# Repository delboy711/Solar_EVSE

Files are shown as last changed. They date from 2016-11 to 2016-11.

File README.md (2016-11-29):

# Solar EVSE
## Description
 This project is intended to manage the charging of an electric car so that the charging current is varied in accordance with available
solar power from a PV array.

## Introduction
Electric cars require an EVSE (Electric Vehicle Supply Equipment) to connect to the domestic electricity supply.  It is the responsibility
 of the EVSE to signal to the car the maximum current it is allowed to draw based on factors like the rating of the domestic wiring, and the cable 
connecting the vehicle to the EVSE.  A smart controller inside the EVSE called an EPC (Electronic Protocol Controller) performs the function by setting the duty cycle on a 12V 
pilot signal sent to the car via the charging cable.  One of the leading models of EPC is manufactured by <a href="https://ecoharmony.co.uk/collections/evse-protocol-controller/products/viridianev-tethered-epc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">Viridian</a> (sometimes labelled as MainPine)
 What makes the Viridian EPC interesting to a DIYer is the fact that the available current signalled to the car can be controlled by applying a voltage on a control pin
 on the Viridian EPC.
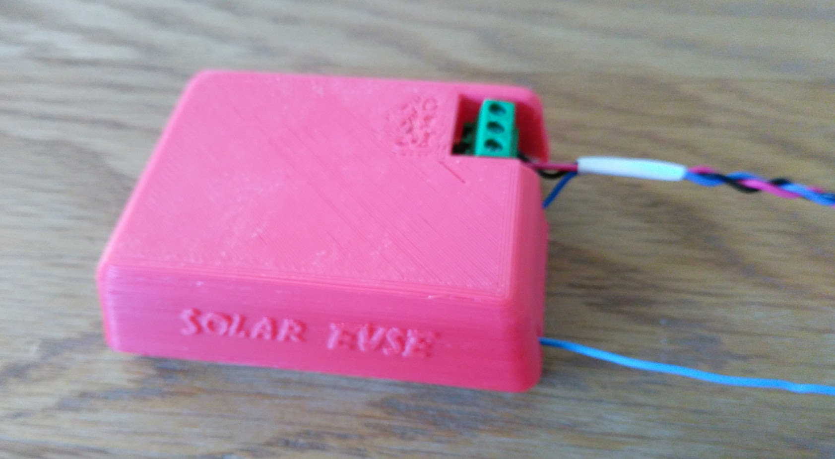
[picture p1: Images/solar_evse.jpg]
Solar EVSE

This project is for an Arduino based device to set that control voltage based on a calculation of available solar power made by an <a href="https://openenergymonitor.org/emon/">OpenEnergyMonitor</a> system, and transmitted
 to the Arduino via a radio link.  The Arduino takes no part in the decision making process. It merely applies the voltage dictated by OpenEnergyMonitor.  The Viridian
 EPC has its own fail safes to prevent an unsafe current being signalled to the vehicle.

## Hardware required is
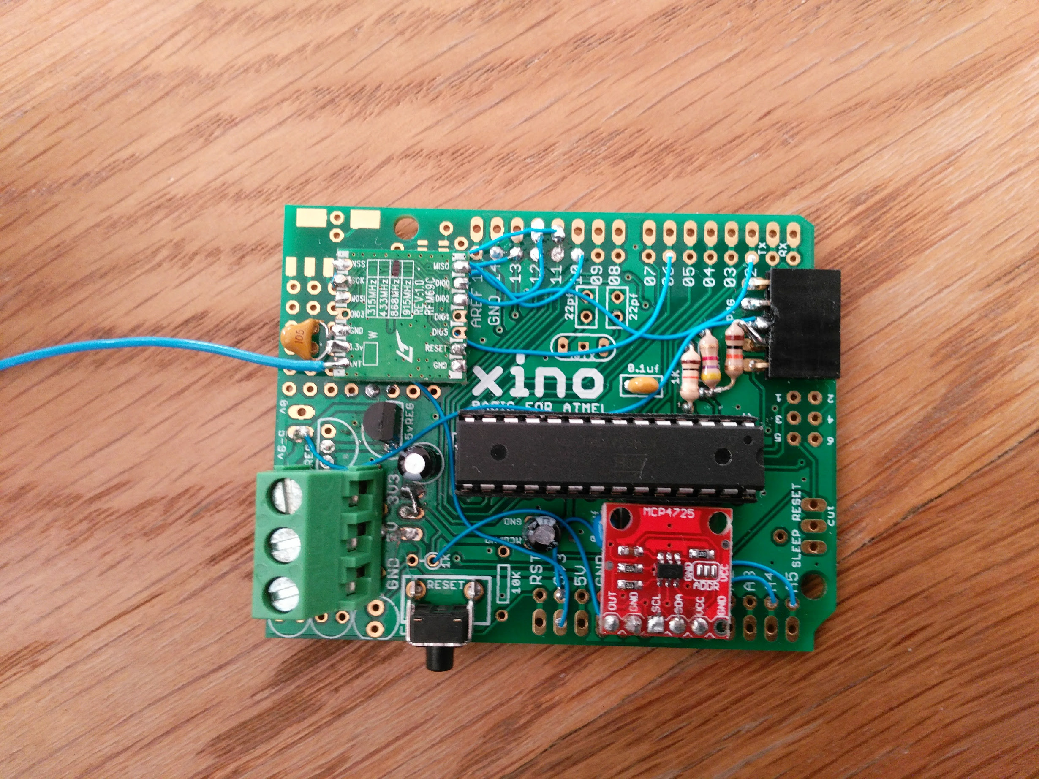
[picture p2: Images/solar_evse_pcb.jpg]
### Arduino Uno -
 or clone, or stripboard with Atmel328P  No crystal required.  I used a <a href="https://nathan.chantrell.net/20110910/xino-basic-arduino-clone/">Xino</a> which is a minimalist Arduino clone with no usb interface, and I 
modfied it to run off 3.3V power which has the advantage of allowing finer control of the Digital to Analogue Converter, and means no step down resistors are required
  for the RFM69CW radio module which requires a 3.3V supply.  By burning a new bootloader into the Atmega328P chip I was able to run it using the <a href="https://www.arduino.cc/en/Tutorial/ArduinoToBreadboard">8MHz internal clock</a> and so saved on the cost of a crystal, and reduced power consumption. Power was drawn from 
the 5V rail of the Viridian EPC itself by wiring in an extra screw connector into the housing of the EPC. Using a Xino at 8MHz the current requirement is 20mA.
* **MCP4725** Digital to Analogue converter module. It is very cheap to buy MCP4725 chips on ebay, ready mounted on a pcb which saves the trouble of trying to solder
surface mount components.
* **RFM69CW** 433MHz or 868MHz radio module. This is the radio module used in the OpenEnergyMonitor project. They are cheap on ebay.
* **Viridian** <a href="https://ecoharmony.co.uk/collections/evse-protocol-controller/products/viridianev-tethered-epc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">Tethered EPC</a>  
                Viridian make their own EVSEs, but I was unable to buy one at a sensible price so instead I bought a <a href="http://www.rolecserv.com/ev-charging/product/EV-Charging-Points-For-The-Home">Rolec EVSE</a> and replaced the Rolec EPC with a Viridian.
Since both the Rolec and Viridian EPCs are DIN rail mounted modules this was a simple exchange.
* **EmonPi or Emonbase** from OpenEnergyMonitor.org
  
## Arduino Libraries required
* **Jeelib**
* **Wire**
* **Adafruit_MCP4725**
  
## Software required
* **Emonhub**
Part of EmonPi or Emonbase. Used to transmit commands over radio link.<br>
A patch is required for emonhub to allow it to transmit control messages to Solar_EVSE. See GitHub for required patch to emonhub.
* **Node-Red**
Included as part of EmonPi.  Used to calculate Solar PV power PV available.
See Node-Red folder for an example flow.
  
## Operation
   This sketch is very simple. The process loops continually waiting for a packet ready flag
   from the RFM69CW radio unit.  When the packet arrives it is validated for CRC and correct address and a single integer
   variable is read.  If the variable has msb bit set, then it is a command to set a new default Power on Voltage for the DAC
   to use. If msb bit is zero it is a new command to set a voltage on the DAC.
   The voltage set on the DAC is passed to the Viridian EPC which uses it to vary the duty cycle
   of the Pilot signal given to an attached electric
   car, and so regulates the current drawn while charging.<br><br>

Installation notes are [here](INSTALLATION.md)

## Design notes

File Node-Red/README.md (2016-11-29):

# Example Node Red flow
In this file is an example flow for Node Red to control a Solar EVSE unit based on available solar power.
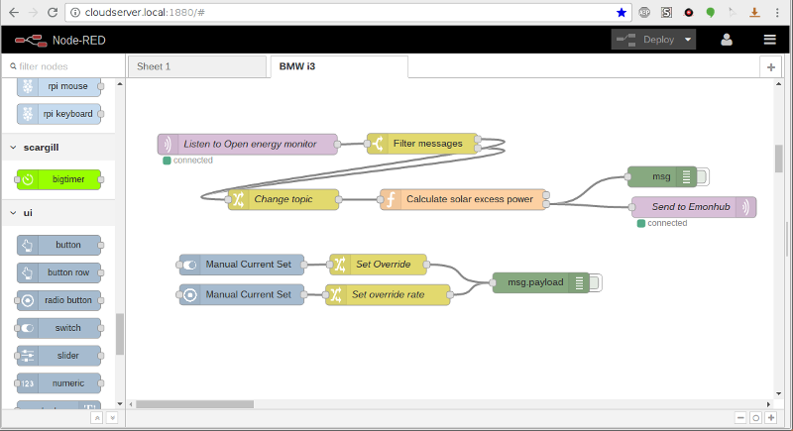
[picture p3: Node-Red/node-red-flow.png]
Node Red flow
To use the flow copy to clipboard and then import into Node Red. 
## Required Nodes
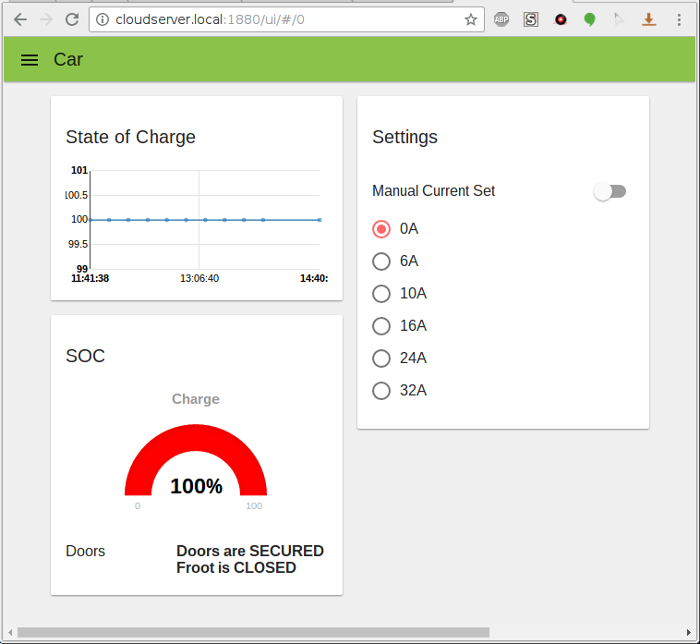
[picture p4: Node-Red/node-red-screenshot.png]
Node Red UI
 This example flow makes use of the [node-red-contrib-ui](https://flows.nodered.org/node/node-red-contrib-ui) node to create a simple user interface to override Open Energy Monitor,
 and set a fixed rate of charge to the vehicle.  In this screenshot are also visible a chart and dial showing vehicle state of charge, These items are not included in
 this flow, and are a separate project.
## Data format
This flow assumes that OpenEnergy Monitor has been configured to provide MQTT messages with the following topics.
* **SMASolar/ACOutputPhase1** - This topic has a payload of output from the solar panels in W. In my system I can read this figure directly from my SMA inverter via a python
 script and Bluetooth.
* **emon/solar_EVSE/car_power** - This topic has a payload of the power being consumed by the car in W.  In my system I derive it from a current sensing transformer
 attached to the EVSE power supply.
* **emon/solar_EVSE/house_power** - This topic has a payload of the total power being consumed in the house, including that consumed by the car.

The flow produces a single output with the topic **emonhub/tx/24/values** which represents the Voltage the Arduino based Solar_EVSE unit should 
 signal to the Viridian EPC. The stanza shown in the emonhub folder should be added to the emonhub.conf file so that emonhub knows what to do with the MQTT message,
 and the patch **EmonHubJeeInterfacer.patch** in the emonhub folder should be applied to emonhub so it can send packets to  remote nodes.
Be aware emonhub is very fussy about receiving properly formatted MQTT packets.  It will crash if it receives a malformed packet.

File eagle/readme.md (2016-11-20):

## Example Schematic
for Solar EVSE mounted on a shield expansion card for an Arduino Uno running at 5V
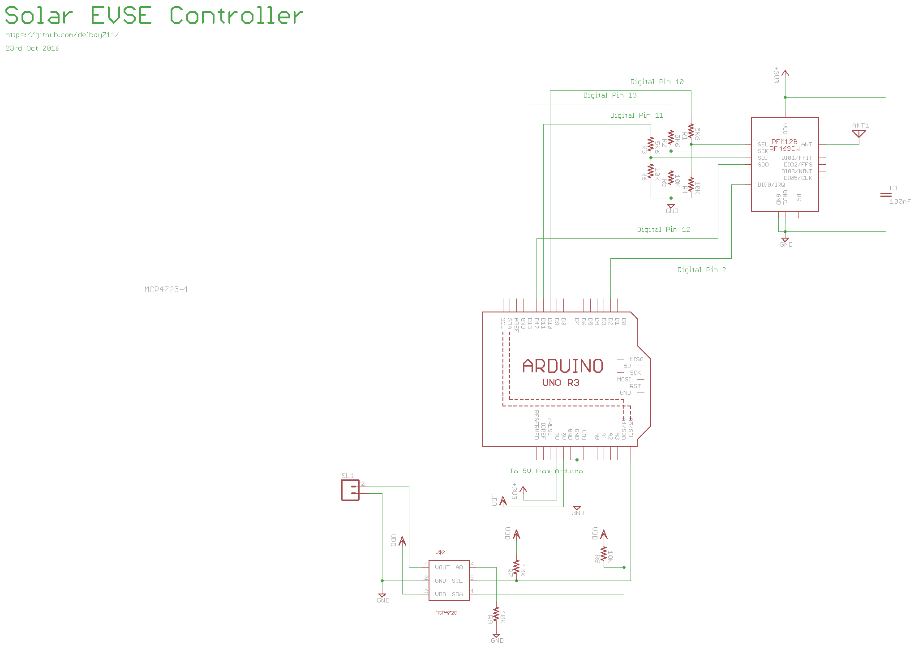
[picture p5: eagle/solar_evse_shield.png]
Arduino shield


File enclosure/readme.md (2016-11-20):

## Files
 for 3D printed enclosure for Solar_EVSE written in OpenSCAD

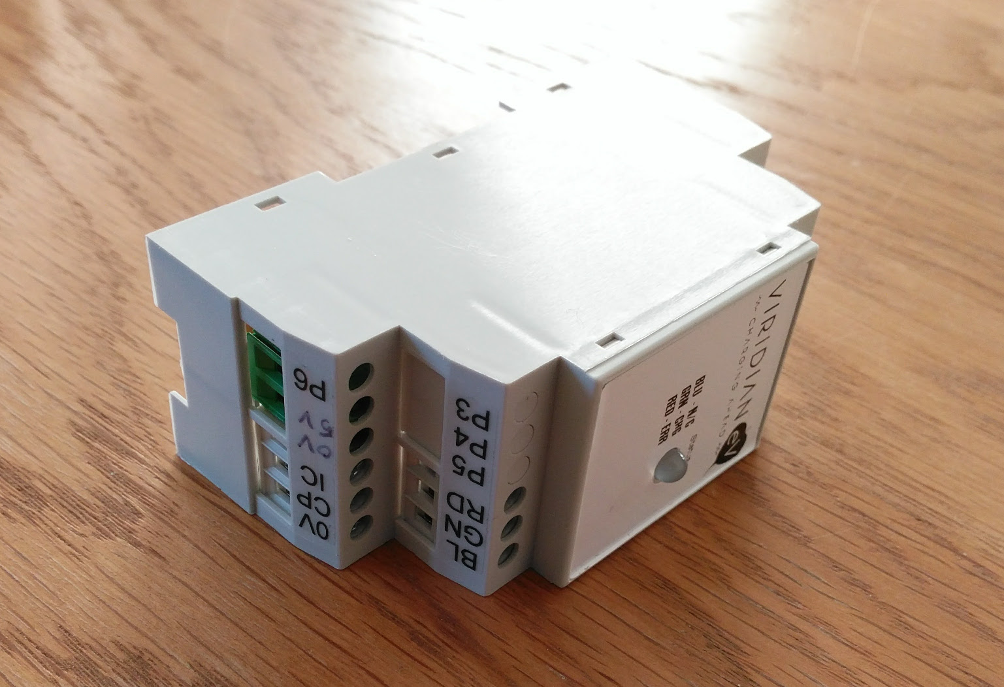
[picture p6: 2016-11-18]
Images/viridian_evse2.jpg

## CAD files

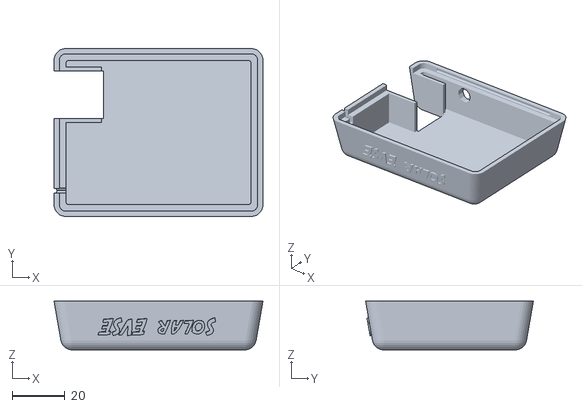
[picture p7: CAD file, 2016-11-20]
enclosure/solarEVSE_top.stl
79.0 x 63.5 x 18.5

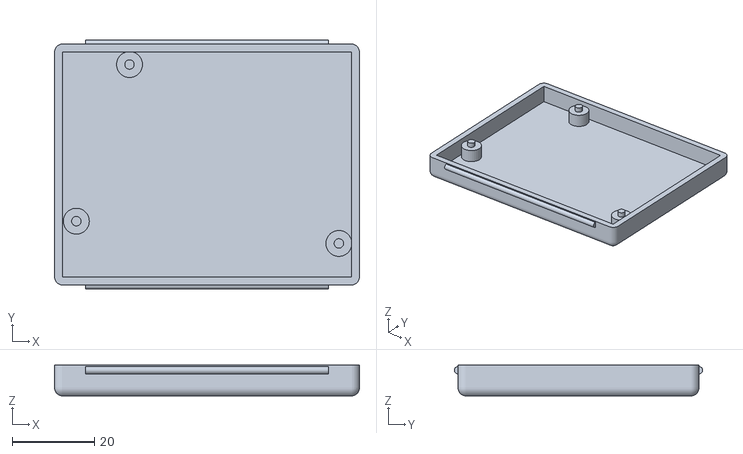
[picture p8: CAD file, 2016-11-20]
enclosure/solarEVSE_bottom.stl
74.0 x 60.3 x 7.49

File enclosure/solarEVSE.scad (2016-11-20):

//
// Arduino Uno
//
// Based on a design by Egil Kvaleberg, 8 Aug 2015
// Remixed by delboy711 21/08/2016

//
// notes:
// design origin is middle of PCB
//



// Set part = "all" to see both top and bottom parts
// Set part = "top" to see just the top part
// Set part = "bottom" to see just the bottom part
// Set part = "demo" to see both parts fitted together
part = "all"; // [ top, bottom, all, demo ]
// Is the Arduino a Uno (USB, and power socket), or a Xino (bare bones no usb or power socket)
// See https://www.wirelessthings.net/xino-basic-for-atmel-atmega-avr-arduino-compatible-kit
device = "Xino";  // [ Uno. Xino ]
// Select feature options
have_emontx_shield =0 ; //Is fitted with an emontx shield card
have_text = 1; //  Writing on side
text_="Solar EVSE";   // Text to write on side
font_size= 7;  // Text font size
have_pcb_fixings = 0; // 
have_snaplock = 1;   // snaplocks on edges
have_bottom_vents = 0;  // Ventilation slots on bottom
have_top_vents = 0;  // Ventilation slots on top
have_cable_outlet= 1; // Has hole for cable outlet
have_screwblock=1;    //Opening for screwblock in lid


/* [Hidden] */
mil2mm = 0.0254;
pcb = [69, 53.5, 1.5]; // main board 
extra_width = 0;   
extra_depth = 0;   // extra space below pcb
extra_length = (have_emontx_shield ? 26 : 0); // extra length Longer with emontx shield fitted
extra_height = (have_emontx_shield ? 9 : 0);   // extra space above pcb taller with emontx shield 
pcb2floor = 4.0 + extra_depth; //  
pcb2roof = 14 + extra_height; //   

pcbmntdia = 2.3; // mounting holes
pcbmntdx= [pcb[0]/2 - 2.5, (device == "Uno" ? 14.5 : 2.8)-pcb[0]/2, pcb[0]/2 - 2.3, pcb[0]/2 - 53.3];  //location of mount holes
pcbmntdy= [7.6 - pcb[1]/2, (device == "Uno" ? 2.8 : 13)-pcb[1]/2, 9.1, pcb[1]/2 - 2.5];

breakaway = 0.3; // have hidden hole for screw, 0 for no extra pegs 
usbsy = 10.5; // core
usbframe = 1.0; // frame
usbsz = 10 + 0.5;
usb1dy = pcb[1]/2 - 15.0;
powerpsx = 9; // power plug width 
powerpsz = 14.0; // plug height
powerssx = 9.9; // power socket width 
powerssz = 10.0; // socket height
powerdz = -1.7; // for plug 
powerdy = 8.8- pcb[1]/2; // 
emonacdz = -3;   // AC power socket of emontx shield
emonacdx = pcb[0]/2 -1.5;
frame_w = 2.5; // width of lip for frame 
snap_dia = 1.8; // snap lock ridge diameter
snapedges = false; // snap lock on all edges or just long ones
//snap_len = 40.0; // snap lock length - no longer used DJ
tol = 0.5; // general tolerance

wall = 2; // general wall thickness  was 1.2 dj
thinwall = 1;   // was 0.4 dj
corner_r = wall; // casing corner radius
corner2_r = wall+tol+wall; // corners of top casing
d = 0.01;
 

module c_cube(x, y, z) {
	translate([-x/2, -y/2, 0]) cube([x, y, z]);
}

module cr_cube(x, y, z, r) {
	hull() {
		for (dx=[-1,1]) for (dy=[-1,1]) translate([dx*(x/2-r), dy*(y/2-r), 0]) cylinder(r=r, h=z, $fn=20);
	}
}

module cr2_cube(x, y, z, r1, r2) {
	hull() {
		for (dx=[-1,1]) for (dy=[-1,1]) translate([dx*(x/2-r1), dy*(y/2-r1), 0]) cylinder(r1=r1, r2=r2, h=z, $fn=20);
	}
}

module bottom() {
	module snap2(ex, both) {
		if (both) translate([pcb[0]/2+tol+wall+ex+extra_length, -(pcb[1]+extra_width-10)/2, wall+pcb2floor+pcb[2]-frame_w/2]) rotate([-90, 0, 0]) cylinder(r=snap_dia/2, h=pcb[1]+extra_width-10, $fs=0.3);
		translate([-(pcb[0]-10)/2, -(pcb[1]/2+tol+wall+extra_width/2), wall+pcb2floor+pcb[2]-frame_w/2]) rotate([0, 90, 0]) cylinder(r=snap_dia/2, h=pcb[0]+extra_length-10, $fs=0.3);
	}
    module plugs(extra) { 
        z0 = wall+pcb2floor+pcb[2];
    }
    module plugs_add() { 
        z0 = wall+pcb2floor+pcb[2];
    }

	module add() {
		hull () for (x = [-1, 1]) for (y = [-1, 1])
			translate([x*(pcb[0]/2+tol+wall-corner_r) + (x>0 ? extra_length : 0), y*(pcb[1]/2+tol+wall+extra_width/2-corner_r), corner_r]) {
				sphere(r = corner_r, $fs=0.3);
				cylinder(r = corner_r, h = wall+pcb2floor+pcb[2]-corner_r, $fs=0.3);
		}
		if (have_snaplock) {
            snap2(0, snapedges);
            rotate([0, 0, 180]) translate([-extra_length,0,0]) snap2(0, snapedges);
        }
	}
	module sub() {
        module pedestal(x, hg, dia) {
            translate([pcbmntdx[x], pcbmntdy[x], wall]) {
				cylinder(r = dia/2+wall, h = hg, $fs=0.2);
                // pegs through pcb mount holes
                if (breakaway > 0) translate([0, 0, hg]) 
                        cylinder(r = dia/2 , h = pcb[2]+d, $fs=0.2);
            }
        }
		difference () {
			// pcb itself
			translate([-(pcb[0]/2+tol), -(pcb[1]/2+tol)-extra_width/2, wall])
				cube([2*tol+pcb[0]+extra_length, 2*tol+pcb[1]+extra_width, pcb2floor+pcb[2]+d]);
			// less pcb mount pedestals 
            for (x = (device=="Xino" ? [0,1,3] :[0:3]))  // leave out one pedestal if xino
                pedestal(x, pcb2floor, pcbmntdia);
            
            // Stop card moving
            if (extra_length > 0 ) translate([pcb[0]/2+0.7,-13,-pcb2floor+3]) cube([3,16,10]);
		}
        
        
        plugs(tol);
        
        
        // DJ Add bottom vents
        if ( have_bottom_vents ) 
            for ( dx=[-4 : 4] ) for ( dy=[-1, 1] ) translate([dx*7, dy*(pcb[1]/2-14), 0]) cube([2, pcb[1]/2-6, 2*wall], center=true);

        
	}
	difference () {
		add();
		sub();
	}
    plugs_add();

    if (part=="all" || part=="demo")  {
       if (device == "Uno") color("LightPink", 0.6) translate([-34,-26.5,6+extra_depth]) scale([10,10,10]) rotate([90,0,0])  import(file="arduino_pcb.stl");
       if (have_emontx_shield) color("LightBlue", 0.6) translate([-12,-26.5,18.5+extra_depth]) scale([0.001,0.001,0.001]) import("emontxshield.stl");
    }
 
}

// Z base is top of pcb
module top() {
	module snap2(ex, both) {
		if (both) translate([pcb[0]/2+tol+wall+ex+extra_length, -(pcb[1]+extra_width-10)/2-tol, -frame_w/2]) rotate([-90, 0, 0]) cylinder(r=snap_dia/2, h=pcb[1]+extra_width-10+2*tol, $fs=0.3);
		translate([-(pcb[0]-10)/2-tol, pcb[1]/2+tol+wall+extra_width/2, -frame_w/2]) rotate([0, 90, 0]) cylinder(r=snap_dia/2, h=pcb[0]+extra_length-10+2*tol, $fs=0.3);
	}
    module plugs(extra) { 
        module usb_plug(dy) {
            translate([-pcb[0]/2, dy, -extra-frame_w]) 
				c_cube(19.9, usbsy+2*extra, usbsz+2*extra+frame_w);
            translate([-pcb[0]/2 -19.9/2, dy, -extra-frame_w]) 
				c_cube(19.9, usbsy+2*usbframe+2*extra, usbsz+2*extra+frame_w+2*usbframe/2);
        }

       // usb plug
       usb_plug(usb1dy);

       translate([-pcb[0]/2 -19.9/2, powerdy , -extra-frame_w]) 
				c_cube(19.9, powerpsx+2*extra, powerpsz+2*extra);
                
    }

	module add() {
		hull () for (x = [-1, 1]) for (y = [-1, 1]) {
			translate([x*(pcb[0]/2+tol+wall-corner_r) + (x>0 ? extra_length : 0), y*(pcb[1]/2+tol+wall+extra_width/2-corner_r), -frame_w]) 
				cylinder(r = corner_r+tol+wall, h = d, $fs=0.3); // include frame
			translate([x*(pcb[0]/2+tol+wall-corner2_r) + (x>0 ? extra_length : 0), y*(pcb[1]/2+tol+wall+extra_width/2-corner2_r), pcb2roof+wall-corner2_r]) 
					sphere(r = corner2_r, $fs=0.3);	
		}
        // Text on side
        if (have_text) {
            translate([extra_length/2, (pcb[1]/2+tol+wall+extra_width/2+0.4),pcb2roof/2 ]) rotate([-100,180,0]) linear_extrude(height = 1.0)  text(text_, font = "Adventure" , size=font_size, halign="center", valign="center");
        }
	}

	module sub() { 

		// room for bottom case within frame 
		hull () for (x = [-1, 1]) for (y = [-1, 1])
			translate([x*(pcb[0]/2+tol+wall-corner_r) + (x>0 ? extra_length : 0), y*(pcb[1]/2+tol+wall+extra_width/2-corner_r), -frame_w-d]) 
                cylinder(r = corner_r+tol, h = d+frame_w, $fs=0.3); 
		// snap lock
        if (have_snaplock) {
            snap2(0, snapedges);
            rotate([0, 0, 180]) translate([-extra_length,0,0]) snap2(0, snapedges);
        }
		difference() { 
			// room for pcb
			translate([0+extra_length/2, 0, -d]) cr_cube(2*tol+pcb[0]+extra_length, 2*tol+pcb[1]+extra_width, d+pcb2roof, 1.0);
			union () { // subtract from pcb:

                // pegs
                if (have_pcb_fixings) for (x = [0:3])  translate([pcbmntdx[x], pcbmntdy[x], 0]) {
                    cylinder(r1 = pcbmntdia/2 +wall, r2 = pcbmntdia/2 +1.5*1.2, h = pcb2roof, $fs=0.2);
                }
                // Screwblock
                if (have_screwblock) translate([-pcb[0]/2+4, -pcb[1]/2+12.5,0]) c_cube(18,21,16);
                       
			}

		}
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

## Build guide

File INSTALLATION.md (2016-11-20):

# Installing Solar EVSE
## Modifying Viridian EPC
To avoid having to have a separate power supply for Solar EVSE, it is easy to modify the Viridian EPC to break out 5v and an additional 0V 
to an additional terminal block.<br>
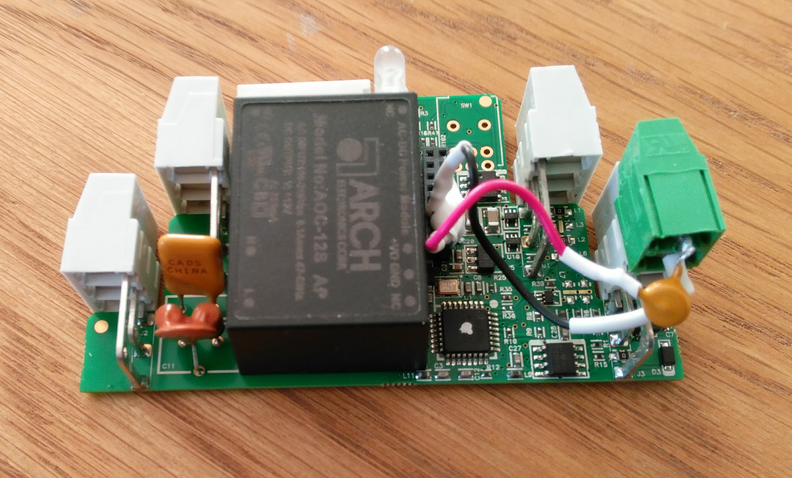
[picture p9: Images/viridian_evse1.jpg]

On opening the EPC it will be seen that there are plastic inserts blanking off the unused terminal positions.
A new two position terminal block can be glued to the side of the existing one, and connections made to +5V and 0V positions on the header connector on the pcb.
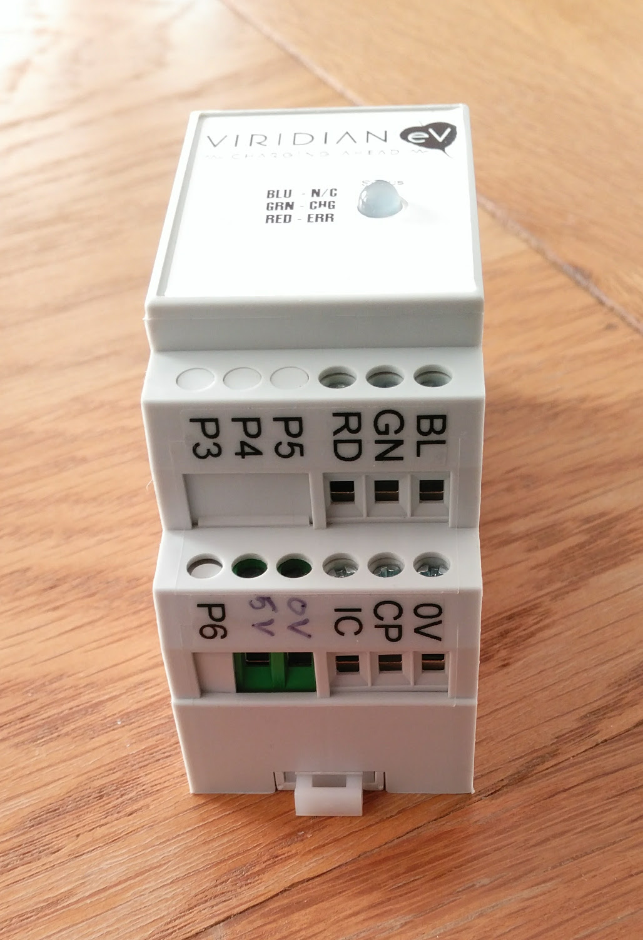
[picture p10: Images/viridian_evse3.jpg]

The 5V connection is on the bottom right of the header.  A spot of silicon keeps the wires in the header.
I routed the 5V wire through an 85mA polyfuse to guard against accidental short circuits.<br>
## Relacing Rolec EPC
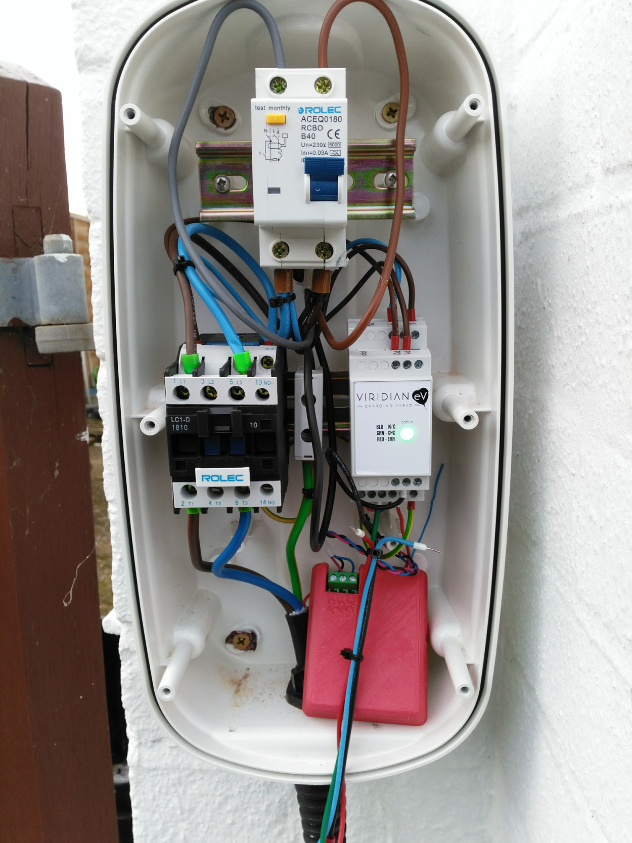
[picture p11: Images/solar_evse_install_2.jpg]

The Vididian EPC is almost but not quite a pin for pin replacement for the Rolec EPC.
Live and Neutral wires go to L and N, the Earth wire that went to the E terminal on the Rolec should be connected to the 0V terminal on the Viridian.
Wires that went to RL1 and RL2 terminals on the Rolec go to to P1 and P2 on the Viridian.<br>
The wire going to the CP pin on the Rolec connects to the CP pin on the Viridian.<br>
### LED Connections
The Rolec and Viridian EPC have their LED connections with opposite polarity so it is not possible to make a pin for pin substitution.
Instead only a single LED can be made to work by taking the black wire that went to 0V on the Rolec and connecting it to the G terminal on the Viridian (for Green LED lighting while charging). The green wire from the fron panel connects to the OV terminal on the Viridian.<br>
### Solar EVSE Connection
From the modified Viridian EPC 5V and 0V are connected to Solar EVSE, and a connection made from the IC terminal to the terminal on Solar EVSE which connects to the output of the DAC.<br>
## Testing
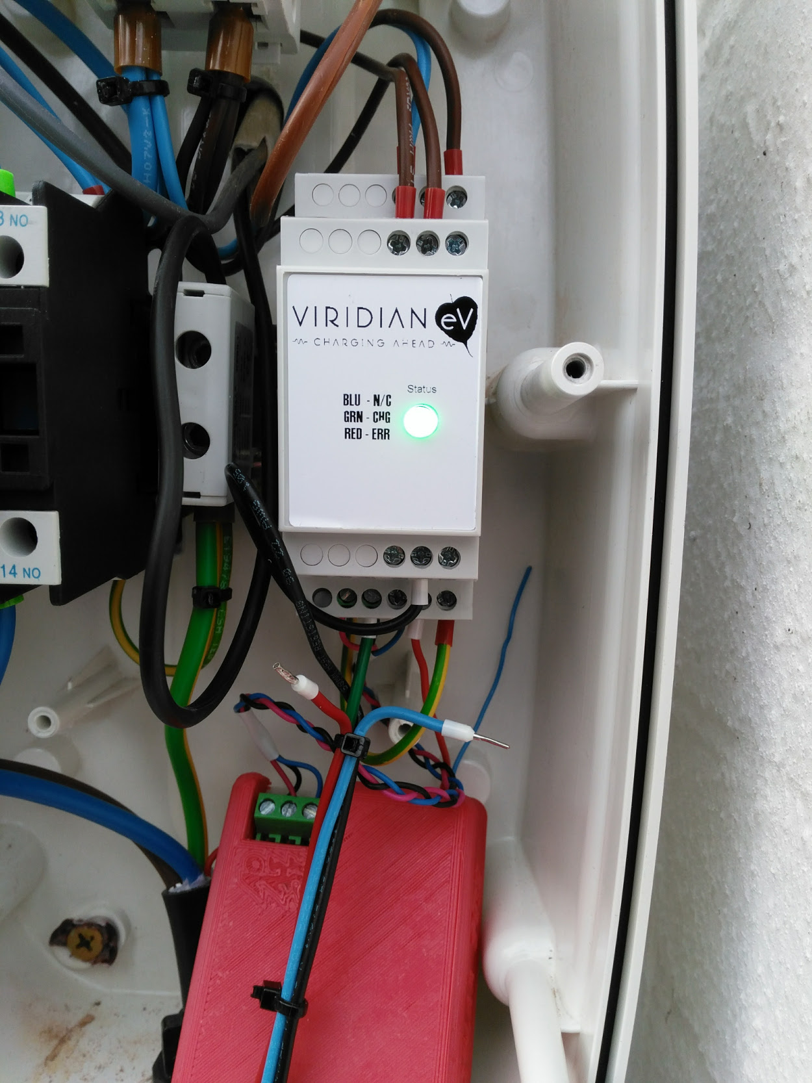
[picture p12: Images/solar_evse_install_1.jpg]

Once Solar EVSE is installed and powered on with the front face off, then it should be possible to use Node Red to send commands to Solar EVSE to set the DAC Voltage. Use DAC settings between around 850 and 2622.  A multimeter connected between IC and 0V on the EPC should show the Voltage changing with each command.
Once a car is connected you should observe different charging rates.<br>
Now all that is required is to define a suitable Node Red flow to manage the rate of charge according to available solar energy.  See the NodeRed folder for details.<br>

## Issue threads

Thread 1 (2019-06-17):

Viridian 5v line

ajaxharg, 2019-06-17:
Hi,
I am making a charger in a similar manner to yourself but am using a photon and some custom software monitoring a solar edge inverter directly.  So many thanks for posting this resource which has been very helpful.

I have pulled apart the viridian and can't seem to see an obvious 5V point to take a power source from which you alluded to in the post.  Is it possible for you to give me a pointer to where that might be please.  Did you power up the device and just poke around with a multimeter?
Cheers
Andy

delboy711, 2019-06-17:
Andy.
Take a look at the image viridian_evse1.jpg in the images folder of this repository. 5v is available on the expansion connector of the Viridian EVSE.  Unfortunately I failed to note down which pin it was and I used silicone goop to hold the wire in place which makes it harder to identify, but you will hopefully be able to find the correct pin.
Glad you found it useful.

Regards. derek

ajaxharg, 2019-06-18:
Hi Derek
thanks for getting back to me.  I hadn't noticed the photos. Cheers for that. It seems mine is different to yours with a split board design with all the pins in use for the bridging.  There isn't much space to solder in.  The 12v line for the solenoid might get activated when the car is plugged in so I might try and use that.
Thanks
Andy

Closed 2019-06-18.

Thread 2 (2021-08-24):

You might want to take a look at my solution to tweak many DC/DC converters like the BST900...

rin67630, 2021-08-24:
My approach is a different one: not reprogram the STM, but replace the board by a TTGO module on a adapter PCB, which provides a gorgeous color display, statistics, Internet dashboard, Telnet and thousands of features...

https://github.com/rin67630/Drok-Juntek-on-steroids
and its application as a solar SCC.
https://github.com/rin67630/Soft-Power2-MPPT

It would be nice to have you on board, we share the same aims,

delboy711, 2021-08-24:
Thanks for the pointer to your project. It looks interesting. When I get the chance I will try it out.  It should certainly be easier than messing about with STM8 assembler.

At first sight the only feature it is missing from my point of view is control/reporting via MQTT so NodeRed can manage it, but that would be easy enough to include.

Regards

Derek

rin67630, 2021-08-24:
Yes I know, MQTT is the golden standard.
I preferred the -admitedly proprietary- approach of the spanish guys at Thinger.io.
It is ways faster and need no additional resource to provide a stunning dashboard.
-no broker, no databse, no Grafana.
...and you can configure your dashboard on-the-fly.

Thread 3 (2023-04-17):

Not working

JVG1989, 2023-04-17:
Hello, I have done it with ESPHome PWM having a voltage between IC and 0V and it does not work. When I introduce for example 1.1V or whatever, relay turns off. In your picture I am not able to see where are you connecting 0Volts apart from the ground

delboy711, 2023-04-17:
Hi
If you are using a PWM signal did you put it through a low pass filter before the IC pin?  It needs a steady DC voltage.

JVG1989, 2023-04-18:
I change the configuration because I suposed that PWM is not lineal and is not valid, so I Put between IC and 0V pins of Viridian DAC output directly from and ESP32 with ESPHome. I double check with multimeter and it is ok. Now with DAC it doesn't turn off, but it doesn't regulate the charging current, it remains lineal.

delboy711, 2023-04-19:
I have never used the DAC in an ESP32 but this link https://www.esp32.com/viewtopic.php?t=5098 suggests it is not very good at sinking current into a pull up resistor like the Viridian has on its IC input.  I suggest you use a multimeter to confirm that the voltage seen on the IC pin is the same as you think the ESP32 is outputting.

It might also be a good idea to check that the IC pin is working correctly by attaching different resistors between IC and OV and confirming the car charges at the correct rate as shown in the Viridian manual https://static1.squarespace.com/static/56274e10e4b05fed125a4df9/t/5e330f8d73b8890fa68a99b3/1580404628132/EVSE_Protocol_Controller_Manual+iss+1.3.pdf

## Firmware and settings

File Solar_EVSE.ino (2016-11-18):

 /*
 * Solar EVSE by Derek Jennings 
 * description:
 * This sketch will regulate a Viridian or Mainpine EPC to modulate
 * the available current available to an Electric Vehicle based on solar PV production.
 *
 * Solar_EVSE receives commands via an RFM69 radio unit from
 * an EmonPi/EmonBase OpenEnergyMonitor system to set a voltage on the control pin
 * of a Viridian EPC which will in turn signal to an Electric Vehicle
 * by varying the duty cycle of the pilot signal to the EV.
 * Node-Red is used within the EmonPi to determine how much power
 * is available from the solar panels after allowing for other loads
 * within the household.
 
 * Hardware required is
 * 	Arduino Uno - or clone, or stripboard with Atmel328P  No crystal required.
 *	MPC4725 Digital to Analogue converter module 
 *	RFM69CW 433MHz or 868MHz radio module 
 *      Viridian tethered EPC  https://ecoharmony.co.uk/collections/evse-protocol-controller/products/viridianev-tethered-epc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
 *              in a suitable EVSE such as an upgraded Rolec
 *      EmonPi or Emonbase from OpenEnergyMonitor.org
 *
 * Libraries required
 *	Jeelib
 *	Wire
 *      Adafruit_MCP4725
 *
 * Software required
 *      Emonhub -   Partof EmonPi or Emonbase. Used to transmit commands over radio link
 *                  See my GitHub for required patch to emonhub.
 *      Node-Red  - Included as part of EmonPi.  Used to calculate Solar PV power PV available.
 *                  See my Githib for an example flow.
 *
 * Operation
 * This sketch is very simple. The process loops continually waiting for a packet ready flag
 * from the RFM69CW radio unit.  When the packet arrives it is validated for CRC and correct address and a simgle integer
 * variable is read.  If the variable has msb bit set, then it is a command to set a new default Power on Voltage for the DAC
 * to use. If msb bit is zero it is a new command to set a voltage on the DAC.
 * The voltage set on the DAC is passed to the Viridian EPC which uses it to vary the duty cycle
 * of the Pilot signal given to an attached electrc
 * car, and so regulates the current drawn while charging.
 */

#include <Wire.h>
#include <Adafruit_MCP4725.h>	    // Get Adafruit_MCP4725 library at https://github.com/adafruit/Adafruit_MCP4725
#define RF69_COMPAT 1               // set to 1 to use RFM69CW
#include <JeeLib.h>		    // Get Jeelib at https://github.com/jcw/jeelib 
#define RF_freq RF12_868MHZ         // Frequency of RF169CW module can be RF12_433MHZ, RF12_868MHZ or RF12_915MHZ. You should use the one matching the module you have.
const int nodeID = 24;              // RFM69 node ID pick an unused nodeID
const int networkGroup = 210;       // RFM69 wireless network group - needs to be same as emonBase and emonGLCD                                                 
boolean debug= true;                // Set to 1 for debug messages
unsigned int dacsetpoint=0;          // Value to put into MCP4725 DAC commanded by Node-Red
unsigned int loopcount=0;            // count of times through main loop 
unsigned int dacmax = 2622;          // max dac setting for 32A

Adafruit_MCP4725 dac;


/* Setup phase */
void setup() {
     
  if (debug) {
    Serial.begin(57600);
    Serial.println("Solar_EVSE controller with Open Energy Monitor"); 
    Serial.print(" Freq: "); 
    if (RF_freq == RF12_433MHZ) Serial.println("433Mhz");
    if (RF_freq == RF12_868MHZ) Serial.println("868Mhz");
    if (RF_freq == RF12_915MHZ) Serial.println("915Mhz");  
  }
  rf12_initialize(nodeID, RF_freq, networkGroup);           // initialize RFM12B/RFM69CW
  if (debug) Serial.println("   :RF Initialized");   
  
  // For MCP4725A1 the address is 0x62 (default) or 0x63 (ADDR pin tied to VCC)
  // For MCP4725A0 the address is 0x60 or 0x61
  // For MCP4725A2 the address is 0x64 or 0x65
  dac.begin(0x60);


}


/* Main loop.*/
void loop() {

   receive_rf_data();                // Has a data packet arrived on the radio?
   delay(500);
   loopcount += 1;                    // increment loop count
   if (loopcount > 7200 ) dac.setVoltage(dacmax, false);    // reset dac to max 32A if no radio message for 1 hour
}  // end main loop


void receive_rf_data()    // Check if a data packet has been received by the radio
{
  int i;
  if (rf12_recvDone()) {
    if (rf12_crc == 0 && (rf12_hdr & RF12_HDR_CTL) == 0)  // and no rf errors
    {
      int node_id_Rx = (rf12_hdr & 0x1F);                  //node ID of received packet
     if (debug) {
       Serial.print("Packet received : Node ");  
       Serial.println(node_id_Rx);
     }
      if (node_id_Rx == nodeID) {
        if (debug) Serial.print("Data received : ");
        dacsetpoint =rf12_data[0]+ 256*rf12_data[1];       // put received data into variable 
        if ( dacsetpoint > 0x7fff ) {                      // If msb set, then save in Flash ROM as new default
          dacsetpoint = dacsetpoint & 0x7fff;              // remove msb bit
          dac.setVoltage(dacsetpoint, true);		   // Write new value to DAC and to ROM         
        } else  dac.setVoltage(dacsetpoint, false);        // Write new value to DAC
        if (debug) {
          Serial.println(dacsetpoint);  
          Serial.print("RSSI : ");                           // Print RSSI value
          Serial.println(-(RF69::rssi>>1));  
          loopcount = 0;                                  // reset loop counter
        }  
      }
    }
  } 
  
} // receive_rf_data

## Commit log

2016-11-02 add schematic
2016-11-18 add timeout
    [solar_EVSE.sch]
2016-11-20 add enclosure
    [solarEVSE.scad, solarEVSE_bottom.stl, solarEVSE_top.stl]
2016-11-20 update schematic
2016-11-22 add Node Red flow
